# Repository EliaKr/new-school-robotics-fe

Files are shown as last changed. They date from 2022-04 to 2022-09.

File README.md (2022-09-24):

# New School Robotics Team - Engineering Materials
This repository contains all information and code necessary to be able to reproduce our FE vehicle's design and function. The files are contained in folders in the main branch, while all info regarding programming and the principles behind the code can be found in this document.

## Table of contents
1. [Introduction](#introduction)
2. [Hardware](#hardware)
    - [Power](#hardwarepower)
    - [Motors](#hardwaremotor)
    - [Control](#hardwarecontrol)
    - [Sensing](#hardwaresensing)
    - [Hardware List](#hardwarelist)
3. [Uploading Code](#upload)
    - [Initial Preparation](#initial)
    - [Client SMB Configuration](#smb)
    - [Connecting via SSH](#ssh)
    - [Useful Commands](#commands)
    - [Notes](#uploadnotes)
5. [Code](#code)
    - [Initial Setup](#codesetup)
    - [Functions](#functions)
    - [Main Code](#maincode)
6. [Bug Fixing](#bugs)
7. [Useful References](#references)
8. [Glossary](#glossary)

## Introduction 
The Future Engineers challenge requires us to build a robot that can complete two tasks. The first task (called the qualifying task) requires the vehicle to make three laps of a square track autonomously, avoiding hitting any walls, as fast as possible and within a period of three minutes. The second task (called the final task) requires the vehicle to make another three laps in the same manner, while also avoiding green and red obstacles in its route and passing them from the correct side, depending on their color.

To accomplish these tasks we built a custom rear-axle driven robot, based on the Raspberry Pi SBC, which allows us to manipulate its motor functions freely, depending on input from numerous sensors located around the front of the vehicle. A wide range of sensors were used, so that the tasks could be completed as efficiently and as fast as possible. These sensors varied from ultrasonic distance sensors to cameras. All systems of the robot were powered by a custom power distribution system, stepping down voltages and supplying power to all components of the robot. Two seperate power systems were created to decrease load and improve performance and reliability, each with its own working voltage, to match the requirements of the devices it powers. In this guide we will go over all the systems in detail and explain the principles and functions behind the code used for the autonomous driving of the robot. Definitions for terms which may be unknown to some readers will be in the end of this guide.

## Hardware 
The hardware used in this project can be divided into four distinct categories. Power, motor, control and sensing hardware. All these systems work together to complete the required tasks. In this section we will look at how each separate category works to support the completed robot. A schematic is available in the `schemes` directory of this repository, to better understand the information in this section and to help you replicate the design on your own. There will also be references to this section in code, so it is possible to refer to this section to understand the working principles behind the code mentioned in [section 4](#code).

### Power Hardware 
The robot is powered from two 18650 lithium ion cells connected in series, with a combined nominal voltage of 7.4V (3.7V each). The output of these cells is distributed to two buck converters, each powered on with a separate switch, which step down the voltage to a stable 5V for the Raspberry Pi and 5.5V for the other components. Each buck converter is rated for up to 3A of current, more than enough for the systems to run without any voltage drops. The 5V buck converter connects directly to the Raspberry Pi 3B+ with a USB cable, while the power from the 5.5V one is distributed using [WAGO terminal blocks](https://cpc.farnell.com/search?st=wago%20terminal&gs=true). The Raspberry Pi is equipped with a [polyfuse](https://elinux.org/Polyfuses_explained) and the 5V step-down converter has an input fuse to protect it from any electrical failures of components connected to GPIO. Both electrical subsystems share a common ground, to enable communication between the digital equipment which use both power sources.

### Motor Hardware 
There is a total of 2 motors on the robot. A NEMA 17 stepper motor is used to drive the back axle. This is connected to a [TMC2209](https://www.trinamic.com/fileadmin/assets/Products/ICs_Documents/TMC2209_Datasheet_V103.pdf) stepper motor driver and allows us to precisely manipulate the speed of the robot and the distance which it travels, by setting the exact number of steps the motor will move at any given time. This drive motor is connected by pulley to a custom made gear on the back axle and features great quiet performance and reliability, making it the best option for its selected purpose. A 9g Metal Gear Servo is used to control the front axle steering of the robot. This motor provides a [holding torque](https://www.motioncontroltips.com/faq-whats-the-difference-between-detent-torque-and-holding-torque/) of around 2.8kg.cm and a speed of approximately 0.09s/60°, making it the perfect motor for use in a steering system. Its high torque and fast response time allow us to have precise and fast steering, a necessity in such a robot. It is controlled using a PWM signal from the GPIO of the Raspberry Pi and is powered from the 5.5V power source.

### Control Hardware 
The Raspberry Pi 3B+ was our SBC of choice for this project. This stems from its great computing capabilities, which are necessary for use with [OpenCV](https://en.wikipedia.org/wiki/OpenCV), the library used for accessing and processing the camera image data. The presence of great documentation for every part of its operation with our code was also a deciding factor in the decision over its use. It has 40 GPIO ports and a dedicated CSI camera connector, making it a great choice for use in such a project. All other components are connected to it via the GPIO, providing useful data and allowing manipulation of motors using code. A button is connected to a GPIO input to give the start signal for the program.

### Sensing Hardware 
In total 7 sensors of 4 different types are used to give the robot information about the track and its location. A camera is used to provide [OpenCV](https://en.wikipedia.org/wiki/OpenCV) with an image of the view from the front of the robot. The camera has an FOV of 160 degrees, giving us a view containing all areas necessary to compute the best path. It is connected to the Raspberry Pi by use of the dedicated CSI connection. Three HC-SR04 Ultrasonic Sensors are present on the robot, one for each side except the back of the robot. They are connected to the Raspberry Pi via the GPIO and a code function is used to calculate the distance from the walls on each side. More information on their working principle can be found [here](https://www.allaboutcircuits.com/industry-articles/understanding-the-basics-of-ultrasonic-proximity-sensors/). Two infrared obstacle sensors, for the left and right sides of the robot, are also present on the robot and could be used for wall detection, even though they are not in the current version of the code due to interference problems. A TCS3200 Color Sensor mounted facing the track under the robot is also present, although this as well is not used for any function as of the latest code version. It could however be used as an alternative way to count the number of laps travelled, by counting the colored lines present on the track surface.

### List of Hardware Used: 
- 1x Raspberry Pi 3B+
- 2x 3400mAh Li-Ion 18650 Battery Cells
- 1x DFRobot DC-DC Fast Charge Module (5V)
- 1x DC-DC Adjustable Buck Converter
- 5x 3-terminal WAGO Terminal Blocks
- 1x 2-terminal WAGO Terminal Block
- 1x TMC2209 Stepper Motor Driver
- 1x NEMA 17 Stepper Motor
- 1x Active Buzzer
- 2x Infrared Obstacle Sensors
- 3x HC-SR04 Ultrasonic Distance Sensors
- 1x 9g Metal Gear Sensor
- 1x TCS3200 Color Sensor
- 1x Raspberry Pi Camera Module 5MP 160°

## Uploading Code 
### Initial Preparation: 
1. Start with the Raspberry Pi turned off.
2. Open a hotspot on your mobile phone or other device with the following characteristics:
- SSID: xxxx
- Password: xxxx
- Security: WPA2-Personal(AES)
- Client Isolation: Off (usually off by default).
3. Initially (optional) power on the motors by turning on the right switch. Then close the left switch, turning on the Raspberry Pi. Automatically the Raspberry Pi will try to connect to the network we created and will start the necessary services for ssh and smb.
4. Using an IP Scanner application ([iPhone](https://apps.apple.com/us/app/ubiquiti-wifiman/id1385561119), [Android](https://play.google.com/store/apps/details?id=com.myprog.netscan&gl=US)) find and note the IP address of the Raspberry Pi. *(In this guide we will denote it as x.x.x.x)*

### Preparing Linux / MacOS systems:
#### - Initial [smb](https://en.wikipedia.org/wiki/Server_Message_Block) configuration for file transfer *(Only once on each network)*: 
1. Open a file browser of your choice. *(In this case Dolphin will be used, but the instructions are the same for all graphical programs.)*



2. Right click on the left bar on the *Remote* or *Network* header of your program. Then select *Add Entry* or an equivalent option. ***(Attention! Click on the header and not on the Network item)***.



3. In the dialog that will appear add a name of your choice, the IP address and the connection protocol in the format `smb://x.x.x.x` and if you want and have the option to do so, select an image for easier identification. In case there is a field for username and passwork enter the following details: `Username: xxx, Password: xxx`.



4. Now there will be an icon in the left bar of our program which will have the name and the image you have chosen. 



5. Clicking on it will bring up a folder. Open it. *(The name will be different)*



6. In the identification dialog that will appear enter the following details: `Username: xxx, Password: xxx` and press *OK* or *Connect*. *(If you have entered them before they may not be requested)*



7. From there go to *Desktop* and from there to the *xxx* folder, where our libraries are downloaded. There you can upload your code to run it in the next part of the guide. *(If you can't see Desktop in this folder, it will be in the home folder.)

#### - Connect via [ssh](https://en.wikipedia.org/wiki/Secure_Shell) to run code: 
1. Open your Terminal program, it will be different depending on the distribution, but the steps remain the same.



2. There execute the command `ssh xxx@x.x.x.x`, where x.x.x.x is the IP address you found in [step 4](#step4) of the initial setup.
3. Immediately afterwards you will be prompted for the password, where you will enter `xxx`.



4. Once you press *Return/Enter* you will be logged in to the Raspberry Pi. Here you can run anything you want on the Raspberry Pi.



5. To find the code you uploaded you need to go to the *xxx* folder in *Desktop*. Do this by using the cd command and more specifically the `cd Desktop/xxx` command.
6. Here you will notice that the working directory has been changed to `~/Desktop/xxx`.



7. From there you can now run the code with the command `sudo python3 xxxx.py`, where `xxxx.py` is the name of the code file. Here you can also run any other command you need to fix your code and the Raspberry Pi.

#### Useful Commands 
- To close the connection run the `exit` command,
- If you want to shut down the Raspberry Pi use the command `sudo shutdown 0`.
- To reboot immediately another useful command is `sudo reboot now`.
- To stop the execution of the code it is sufficient to use the keybind `Ctrl+C`

#### Notes 
- Details denoted with `xxx` need to be filled in by the user.

## Code 
The code file that runs on the robot can be found at `src/xfinal.py`. To run it 6 libraries are required. These libraries are contained in the `/src/libraries/` folder and consist of time, numpy, OpenCV, dlib, TMC_2209 and RPi.GPIO. The `xfinal.py` file contains all the code needed to complete all the tasks required by the Future Engineers competition regulations. In this section we are going to explain in detail every section of the code and how it all works to accomplish the goal required.

### Initial Setup 
Lines 1-69 of the code contain all the code required to initialize the robot's systems and prepare the GPIO pins for the next code sections. In more detail:
- Lines 1-5 `import` the necessary libraries for the code to work.
- Line 6 `GPIO.setmode(GPIO.BCM)` declares the GPIO pin numbering system used in the program.
- Lines 9-18 declare integrers that contain the GPIO pin numbers for all devices that use GPIO. This is done for easier and more efficient coding in the following sections.
- Lines 21-30 `setup` the GPIO pins as inputs and outputs, while also enable the internal pull down resistor of pin 27, the pin used for the button.
- Lines 34-47 `set` the parameters used for stepper motor operations, like the microstepping resolution, max current, acceleration and speed.
- Line 49 enables the motor with the command `tmc.setMotorEnabled(True)`
- Lines 52-53 enable the PWM output of pin 17, where the servo is connected, thus enabling the servo.
- Lines 55-69 contain the parameters for the OpenCV `masks` used for isolating the red and green colors later in the code. Isolating the colors allows us to measure their prevalence in the image and adjust the robot's movement accordingly.

### Functions 
The code is written in such a way where most code is contained in pre-defined functions, which are called in the main loop. These functions enable control of the robot and use of sensor data. They are defined in lines 72-169.
- Lines 72-109 contain the functions for distance measurement using the ultrasonic sensors placed in the front, left and right sides of the robot. These sensors work on the principle of measuring the time between the transmission of an ultrasonic pulse and the receipt of its echo in the sensor. The functions measure the amount of time taken and perform all the necessary calculations to convert it to a centimeter `distance` output.
- Lines 111-123 contain the functions for the operation of the steering servo motor. Steering the robot is accomplished by changing the duty cycle of the `PWM` output of the servo pin, thus instantly changing the direction of the steering servo motor.
- Lines 126-139 define the functions used for the robot's linear movement. The back-axle stepper motor is controlled with the `tmc.runToPositionSteps` command, which allows us to precisely define the steps and consequently the angle the motor will travel in a single movement. This allows us to control the exact distance the robot will travel during any movement.
- Lines 141-169 contain the functions used for detecting the presence of the red and green obstacles in front of the robot. This is accomplished by use of a mask for each color and calculation of the presence of each color in the image, by calculating the number of pixels covered by the mask. These functions return a `True` or `False` boolean value, which is used in the main loop.

### Main Code 
The main code section, in lines 172-212, contains a loop, which works to check the values of the robot's sensor and camera inputs and manipulate the robot's movement in such a way to accomplish the WRO Future Engineers tasks. This loop repeats until the robot has completed 3 revolutions. Detection of the revolutions is done by use of a counter that raises by one in value when the robot makes a turn at a corner.

While this counter indicated that less than 3 revolutions have been completed the robot takes constant measurements of the distance measured by each of the 3 ultrasonic sensors and when there is free space in front of it it keeps going `forward()`. When a wall is detected the robot completes a turn to the direction where it detects is should go. This detection is done by measuring the distance on each side and turning to the one with the most space. This ensures that the robot can complete both the qualifying and final rounds, no matter the direction in which it was initially placed. 

When completing the movement it also checks for the presence of obstacles in front of it and moves accordingly. The detection of obstacles works by checking the output of the OpenCV functions described in the previous sections. There is also wall detection by measuring the distance to the walls. If the distance is smaller than the threshold the robot turns away from the wall automatically. 

## Bug Fixing 
- **The motor doesn't operate normally, it runs in a random direction every time:** Make sure that the login shell over serial is disabled, then reboot.
- **The ultrasonic sensors aren't calculating the distance to the walls:** Remove the function containing the sensor code and use its code directly in the main loop.

## Useful References 
1. [TMC_2209 Raspberry Pi Library GitHub](https://github.com/Chr157i4n/TMC2209_Raspberry_Pi)
2. [Wiring Schematic](https://github.com/EliaKr/new-school-robotics-fe/blob/main/schemes/schematic.pdf)
3. [TMC2209 Datasheet](https://www.trinamic.com/fileadmin/assets/Products/ICs_Documents/TMC2209_Datasheet_V103.pdf)
4. [BigTreeTech TMC2209 Github](https://github.com/bigtreetech/BIGTREETECH-TMC2209-V1.2)

## Glossary 
- FE: The Future Engineers category of the World Robotics Olympiad
- Main Branch: The main branch of this github repository
- SBC: Single Board Computer
- Buck Converter: A device which takes in a higher voltage and converts it to a lower one by use of efficient rapid switching.
- WAGO Terminal Blocks: A type of cage clamp connector which allows for easy reversible connection splicing.
- Polyfuse: A type of self-resettable fuse made out of polymer.
- GPIO: The General Purpose Input and Output pins of the Raspberry Pi. They allow for control of other hardware via a variety of modes, such as PWM and I2C, but also typical analog and digital operation.
- Stepper Motor: A type of brushless motor allowing the user to precisely define its angle and speed of rotation.
- Servo Motor: A type of motor which allows the user to define the angle at which it is positioned by use of a PWM signal.
- FOV: Field of View, a measure of the area covered by the camera.

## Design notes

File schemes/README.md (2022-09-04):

Electromechanical diagrams
====

This directory contains a schematic diagram of the electromechanical components illustrating all the elements (electronic components and motors) used in the vehicle and how they connect to each other.

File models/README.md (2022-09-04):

# Custom 3D Models
This folder contains the .stl files for the custom 3d models modified or designed by us for 3D Printing.

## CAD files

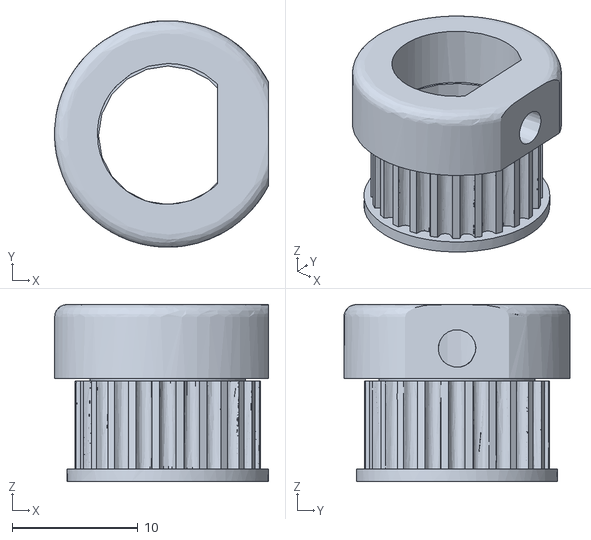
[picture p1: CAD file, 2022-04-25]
models/back-axel-custom-gear.stl
17.0 x 18.0 x 14.1

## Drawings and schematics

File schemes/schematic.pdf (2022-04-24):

7.4-8.4V

## 3400mAh

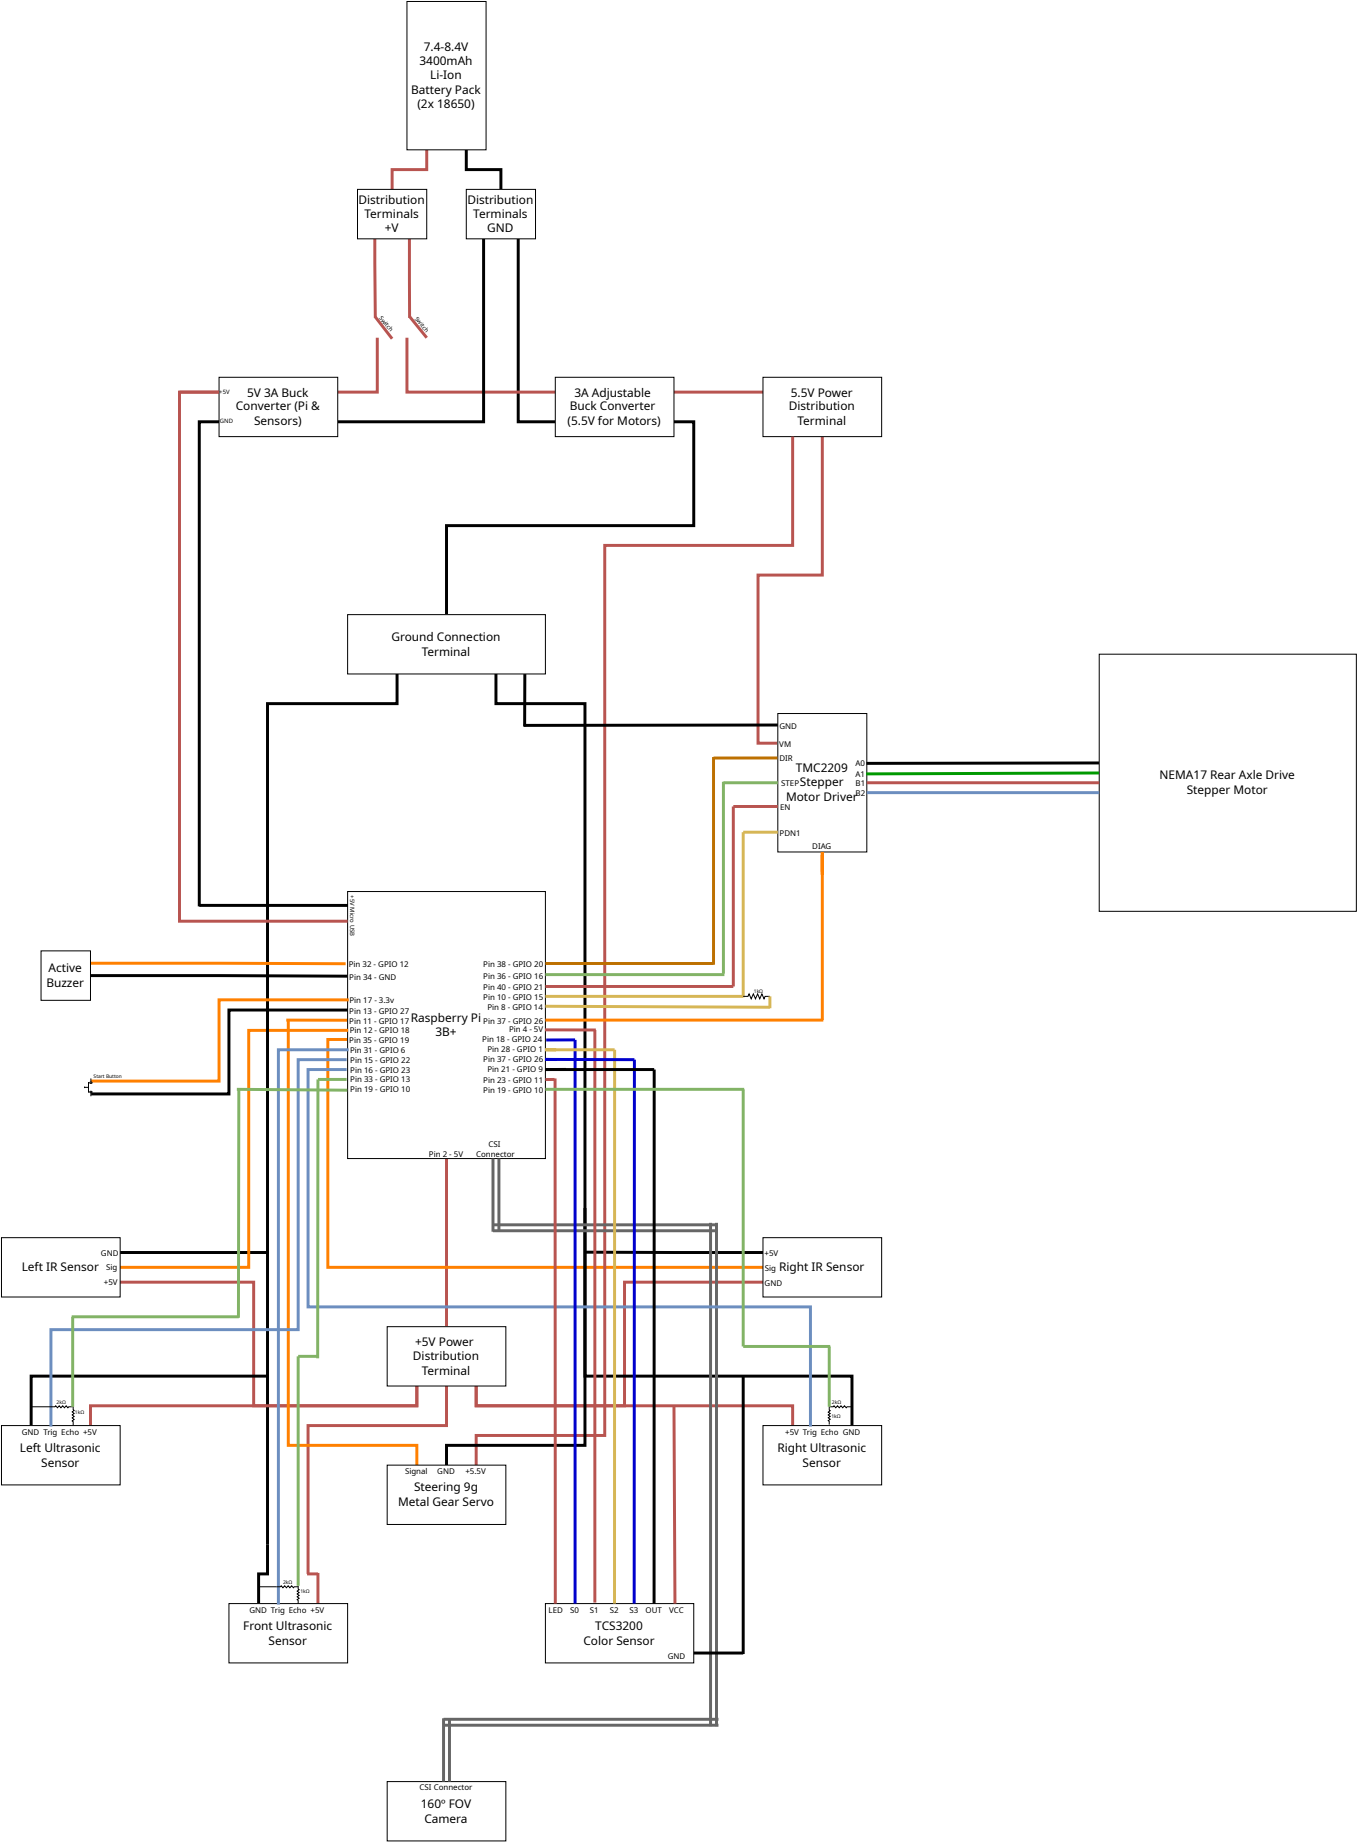
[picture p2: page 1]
Raspberry Pi 3B+; Left IR Sensor; Right IR Sensor; Front Ultrasonic Sensor; Left Ultrasonic Sensor; Right Ultrasonic Sensor; Li-Ion Battery Pack (2x 18650); 3A Adjustable Buck Converter (5.5V for Motors); 5V 3A Buck Converter (Pi & Sensors); 5.5V Power Distribution Terminal; +5V Power Distribution Terminal; Ground Connection Terminal; Distribution Terminals +V; Distribution Terminals GND; Switch; Switch TMC2209; Stepper Motor Driver; Active Buzzer; 160º FOV Camera; GND; +5V Micro USB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

NEMA17 Rear Axle Drive
Stepper Motor

GND +5.5V
Steering 9g
Metal Gear Servo

LED S0 S1 S2 S3 OUT VCC
TCS3200
Color Sensor

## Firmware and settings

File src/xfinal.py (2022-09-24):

from TMC_2209.TMC_2209_StepperDriver import *
import time
import RPi.GPIO as GPIO
import cv2
import numpy
GPIO.setmode(GPIO.BCM)

# define GPIO pins
lefttrig = 22
leftecho = 4
righttrig = 23
rightecho = 10
fronttrig = 6
frontecho = 13
servo = 17
leftir = 18
rightir = 19
button = 27

# set up GPIO pins
GPIO.setup(lefttrig,GPIO.OUT)
GPIO.setup(leftecho,GPIO.IN)
GPIO.setup(righttrig,GPIO.OUT)
GPIO.setup(rightecho,GPIO.IN)
GPIO.setup(fronttrig,GPIO.OUT)
GPIO.setup(frontecho,GPIO.IN)
GPIO.setup(servo,GPIO.OUT)
GPIO.setup(leftir,GPIO.IN)
GPIO.setup(rightir,GPIO.IN)
GPIO.setup(27, GPIO.IN, pull_up_down=GPIO.PUD_DOWN)

# initiate the TMC_2209 class
# use your pins for pin_step, pin_dir, pin_en here
tmc = TMC_2209(16, 20, 21)

# these functions change settings in the TMC register
tmc.setDirection_reg(True)
tmc.setVSense(True)
tmc.setCurrent(400)
tmc.setIScaleAnalog(True)
tmc.setInterpolation(True)
tmc.setSpreadCycle(False)
tmc.setMicrosteppingResolution(16)
tmc.setInternalRSense(False)

tmc.setAcceleration(16000)
tmc.setMaxSpeed(5000)

tmc.setMotorEnabled(True)

# Start Servo
pwm=GPIO.PWM(servo, 50)
pwm.start(0)

# Red Mask
lower_red = np.array([0,50,50])
upper_red = np.array([10,255,255])
maskred0 = cv2.inRange(img_hsv, lower_red, upper_red)

lower_red = np.array([170,50,50])
upper_red = np.array([180,255,255])
maskred1 = cv2.inRange(img_hsv, lower_red, upper_red)

maskred = maskred0+maskred1

# Green Mask
lower_green = np.array([65,60,60])
upper_green = np.array([80,255,255])
maskgreen = cv2.inRange(img_hsv, lower_red, upper_red)

# Define Main Functions
def rightus():
    GPIO.output(righttrig, True)
    time.sleep(0.00001)
    GPIO.output(righttrig, False)
    while GPIO.input(rightecho)==0:
        pulse_start = time.time()
    while GPIO.input(rightecho)==1:
        pulse_end = time.time()
    pulse_duration = pulse_end - pulse_start
    distance = pulse_duration * 17150
    distance = round(distance, 2)
    return(distance)

def leftus():
    GPIO.output(lefttrig, True)
    time.sleep(0.00001)
    GPIO.output(lefttrig, False)
    while GPIO.input(leftecho)==0:
        pulse_start = time.time()
    while GPIO.input(leftecho)==1:
        pulse_end = time.time()
    pulse_duration = pulse_end - pulse_start
    distance = pulse_duration * 17150
    distance = round(distance, 2)
    return(distance)

def frontus():
    GPIO.output(fronttrig, True)
    time.sleep(0.00001)
    GPIO.output(fronttrig, False)
    while GPIO.input(frontecho)==0:
        pulse_start = time.time()
    while GPIO.input(frontecho)==1:
        pulse_end = time.time()
    pulse_duration = pulse_end - pulse_start
    distance = pulse_duration * 17150
    distance = round(distance, 2)
    return(distance)

def left():
    pwm.ChangeDutyCycle(5) # left full position

def softleft():
    pwm.ChangeDutyCycle(6.5)

def center():
    pwm.ChangeDutyCycle(7.78) # neutral position

def softright():
    pwm.ChangeDutyCycle(8.5)

def right():
    pwm.ChangeDutyCycle(10) # right full position

def forward():
    tmc.runToPositionSteps(6000, MovementAbsRel.relative)

def fullforward():
    tmc.runToPositionSteps(25500, MovementAbsRel.relative)

def backward():
    tmc.runToPositionSteps(-6000, MovementAbsRel.relative)

def half_back():
    tmc.runToPositionSteps(3000, MovementAbsRel.relative)

def half_forward():
    tmc.runToPositionSteps(-3000, MovementAbsRel.relative)

def checkred():
    success, img = cam.read()
    kernel2 = np.ones((5, 5), np.float32)/25
    img = cv2.filter2D(src=image, ddepth=-1, kernel=kernel2)
    img = cv.Flip(img, flipMode=-1)
    left = img[0:240, 200:600]
    output_img = left.copy()
    output_img[np.where(maskred==0)] = 0
    allpix = np.sum(output_img <= 255)
    blackpix = np.sum(output_img < 35)
    if blackpix < (allpix / 3):
        return(True)
    else:
        return(False)

def checkgreen():
    success, img = cam.read()
    kernel2 = np.ones((5, 5), np.float32)/25
    img = cv2.filter2D(src=image, ddepth=-1, kernel=kernel2)
    img = cv.Flip(img, flipMode=-1)
    right = img[240:480, 200:600]
    output_img = right.copy()
    output_img[np.where(maskgreen==0)] = 0
    allpix = np.sum(output_img <= 255)
    blackpix = np.sum(output_img < 35)
    if blackpix < (allpix / 3):
        return(True)
    else:
        return(False)

# Main Code
while True:
    if GPIO.input(27) == GPIO.HIGH:
        turns = 0
        while turns < 12:
            front = frontus()
            distright = rightus()
            distleft = leftus()
            if front >= 101 and distright >= 3 and distleft >= 3:
                forward()
                red = checkred()
                green = checkgreen()
                if red == True:
                    right()
                    forward()
                    center()
                elif green == True:
                    left()
                    forward()
                    center()
                else:
                    print("No Obstacles Detected")
            elif distright < 3:
                left()
                forward()
                center()
            elif distleft < 3:
                right()
                forward()
                center()
            else:
                if distright > distleft:
                    right()
                    fullforward()
                    center()
                    turns = turns + 1
                else:
                    left()
                    fullforward()
                    center()
                    turns = turns + 1

tmc.setMotorEnabled(False)
del tmc

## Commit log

2022-04-24 Added robot schematic
2022-04-25 Added custom gear 3d model
    [back-axel-custom-gear.stl]
2022-05-12 Added ir sensor and button start functionality
2022-05-13 Add returning steering to neutral after turning and fixed turning on wall detection
2022-05-18 Added alternate code
    Solves problems with ultrasonic sensor readings over 30 degrees
2022-05-23 added camera code
2022-05-23 added code to camera
2022-05-24 Added first version of camera code
